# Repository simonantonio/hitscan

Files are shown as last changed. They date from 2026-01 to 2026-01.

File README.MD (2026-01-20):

# Project Hitscan

Hitscan logo

An attempt at a super cheap time keeping system for racers
It uses IR diodes on a drone, and a detection station to track when the drone passes the detector.

*Should?* be good at up to speeds of 200km/hr with a 200mm detection window - (need to actually validate this)

### IR Details
**Packet timing now:**

* SYNC: 270μs burst + 900μs gap = 1170μs
* 3 bits: ~300-600μs each = ~1200μs average
* **Total: ~2.3ms per packet**

**At 200mm cone width:**

* 100 km/hr (27.78 m/s): 7.2ms window = 3 packets ✅
* 150 km/hr (41.67 m/s): 4.8ms window = 2 packets ✅
* 200 km/hr: 3.6ms window = 1 packet ✅

> [!CAUTION]
> In development

Initial project is currently in the mail from the board fab.

## Tools

* Kicad 9.0 for board development
* PlatformIO for firmware builds and deployment

## Firmware
* [Base station](./hitscan-base/README.MD)
* [IR Blaster](./hitscan/README.MD)

### Web App
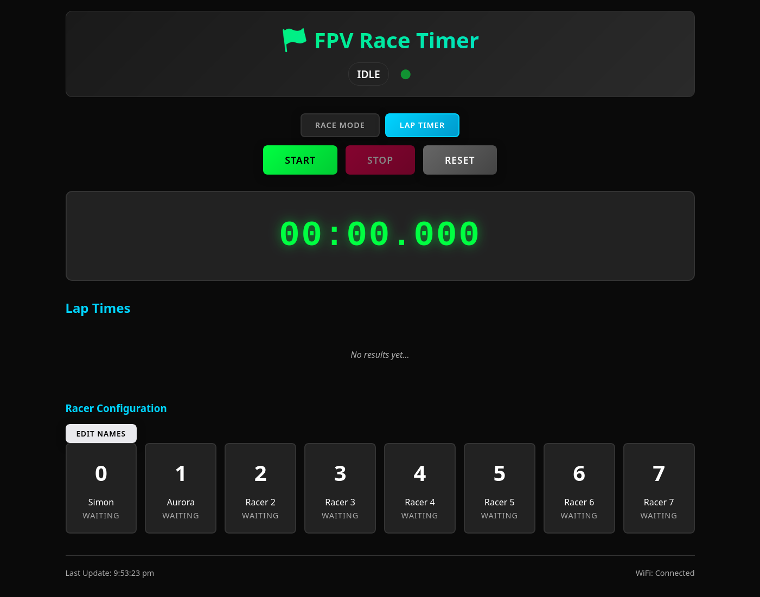
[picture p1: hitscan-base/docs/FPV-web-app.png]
Web app


## Hardware
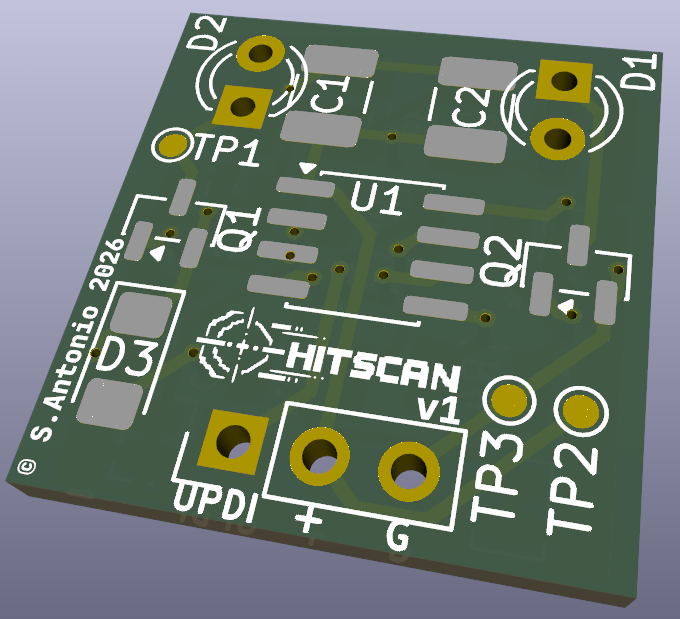
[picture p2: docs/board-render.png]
Board render


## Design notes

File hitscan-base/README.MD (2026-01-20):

# Hitscan base station

Runs on an ESP32 with Audio feedback, LED lights for status's and web app for tracking lap times
Mount your hitscan pcb on your quad with led's facing left/right on the quad. So tracking will work in either direction

Web app screenshot in Lap mode

> [!NOTE]
> Requires a 3d model (to be designed)

> [!WARNING]
> to be validated with actual hardware (PCB is in production)

> [!CAUTION]
> In development

## Thoughts
* Gate to be a tunnel looking at center at least 200mm long - thinking pvc pipe maybe. - ideally integrated with print
* runs IR detection on second core so it minimizes chances of missing a detection

## BOM
* [ESP32 Dev Kit](https://s.click.aliexpress.com/e/_c3kfkJBp) - any ESP32 dev board will do - you may have to tweak pins
* [MAX98357](https://s.click.aliexpress.com/e/_c2RRIQvD) - Class D Amplifier
* [Micro SD SPI breakout](https://s.click.aliexpress.com/e/_c3Uia44J)
* [16 Segment Pixel Ring](https://s.click.aliexpress.com/e/_c42eBGlp)
* [38khz TSOP4838](https://s.click.aliexpress.com/e/_c31xNmn9) - IR sensor

### Wiring diagram

> [!NOTE]
> TODO!

## Setup

### Environment
Set your local wifi password in `.env` file located alongside this readme

example:
```
WIFI_SSID=YOUR_HOME_NETWORK
WIFI_PASS=SUPER_SECURE_PASSWORD
```

### SPIFFS
Load the web app via platformio's `Build Filesystem Image` and `Upload Filesystem Image`

## Running

You can either navigate to .local or the devices ip, or you can connect to the hot spot created and connect there via browser

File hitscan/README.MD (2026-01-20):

# Hitscan board

> [!CAUTION]
> In development

This board gets mounted on your quad with +5v and GND, it emits a signal for up to 8 racers

Runs on ATTiny402 - fits on a 17.5mm x 18.5mm board

## Setup

Make sure to flash each pcb with different racer id

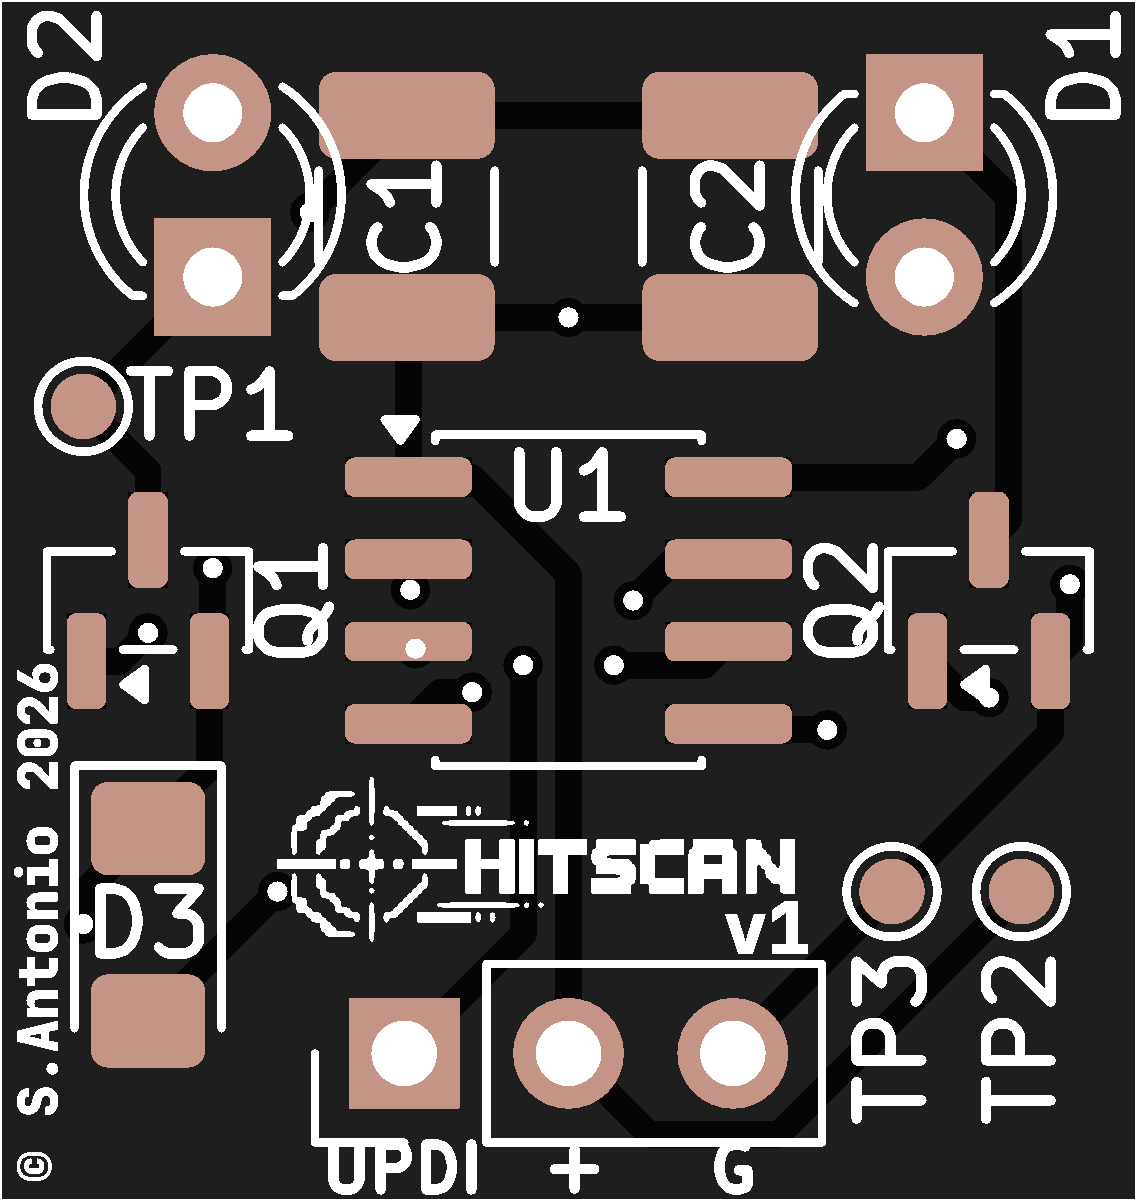
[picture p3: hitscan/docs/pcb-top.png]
PCB top


## What this firmware does

Blasts a single code for a racer over and over, ideally so when we cross our detection window we get at least 3 clean reads at speeds up to 200km/hr

Probably wont work outside in the sun.

## BOM
* [AO3400](https://s.click.aliexpress.com/e/_c3vhLHiB) - Mosfet to drive IR LEDs
* [TSAL4400](https://s.click.aliexpress.com/e/_c3m8pfAJ) - IR LED 100mA
* [ATTiny402](https://s.click.aliexpress.com/e/_c3q55ecr) - 8 pin 20mHz microcontroller
* [1210 SMD Resistors](https://s.click.aliexpress.com/e/_c2uIW28f) - misc resisters
* [UPDI Friend](https://s.click.aliexpress.com/e/_c4tdFiLV) - optional programmer for ATTiny
* [1210 Ceramic Capacitor](https://s.click.aliexpress.com/e/_c4kVavzV) - 0.1uF capacitor
* [1210 Ceramic Capacitor](https://s.click.aliexpress.com/e/_c3ftnBcb) - 100uF capacitor
* [1206 LEDs](https://s.click.aliexpress.com/e/_c4UlNysX) - optional colored LED for status

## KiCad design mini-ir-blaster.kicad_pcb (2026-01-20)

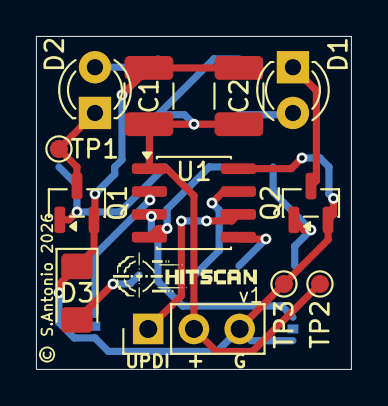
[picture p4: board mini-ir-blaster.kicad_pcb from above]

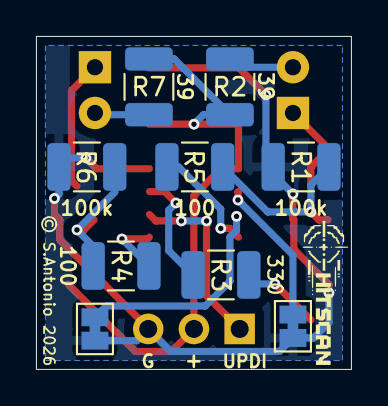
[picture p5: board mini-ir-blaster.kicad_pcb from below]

Board: 2 copper layers, 17.5 x 18.5 mm, 21 parts (9 on the bottom side), 15 nets.

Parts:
C1: 10uF; C_1210_3225Metric_Pad1.33x2.70mm_HandSolder
C2: 0.1uF; C_1210_3225Metric_Pad1.33x2.70mm_HandSolder
D1, D2: TSAL4400; LED_D3.0mm_IRBlack
D3: LED; LED_1206_3216Metric_Pad1.42x1.75mm_HandSolder
J1: Conn_01x03_Pin; PinHeader_1x03_P2.54mm_Vertical
JP2, JP3: Jumper_2_Bridged; SolderJumper-2_P1.3mm_Bridged_Pad1.0x1.5mm
Q1, Q2: AO3400A; SOT-23
R1, R6: 100k; R_1210_3225Metric_Pad1.30x2.65mm_HandSolder
R2, R7: 39; R_1210_3225Metric_Pad1.30x2.65mm_HandSolder
R3: 330; R_1210_3225Metric_Pad1.30x2.65mm_HandSolder
R4, R5: 100; R_1210_3225Metric_Pad1.30x2.65mm_HandSolder
TP1: IR1TP; TestPoint_Pad_D1.0mm
TP2: +TP; TestPoint_Pad_D1.0mm
TP3: GNDTP; TestPoint_Pad_D1.0mm
U1: ATtiny402-SS; SOIC-8_3.9x4.9mm_P1.27mm

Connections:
+5V: C1.1, C2.1, J1.2, R2.1, R7.1, TP2.1, U1.1 (VCC)
/PA1: R5.1, U1.4 (PA1)
/PA2: R4.1, U1.5 (PA2)
/UPDI: J1.1, U1.6 (~RESET/PA0)
GND: C1.2, C2.2, D3.1 (K), J1.3, JP2.2 (B), JP3.2 (B), Q1.2 (S), Q2.2 (S), R1.1, R6.1, TP3.1, U1.8 (GND)
unnamed: D1.2 (A), R7.2
unnamed: D1.1 (K), Q2.3 (D)
unnamed: D2.2 (A), R2.2
unnamed: D2.1 (K), Q1.3 (D), TP1.1
unnamed: D3.2 (A), R3.2
unnamed: JP2.1 (A), U1.2 (PA6)
unnamed: JP3.1 (A), U1.3 (PA7)
unnamed: Q1.1 (G), R1.2, R5.2
unnamed: Q2.1 (G), R4.2, R6.2
unnamed: R3.1, U1.7 (PA3)

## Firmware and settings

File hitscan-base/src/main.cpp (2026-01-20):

#include <Arduino.h>
#include "RaceTimerSystem.hpp"

// Pin definitions
#define IR_PIN 23
#define LED_PIN 25
#define I2S_BCK 26
#define I2S_WS 27
#define I2S_DATA 14

// WiFi credentials
const char *AP_SSID = "RaceTimer-01";  // Direct connection AP
const char *AP_PASSWORD = "racing123"; // AP password (min 8 chars)
const char *STA_SSID = WIFI_SSID;
const char *STA_PASSWORD = WIFI_PASS;

RaceTimerSystem raceTimer(IR_PIN, LED_PIN, I2S_BCK, I2S_WS, I2S_DATA);

void heartBeat()
{
  pinMode(2, OUTPUT);

  // thump
  for (int i = 0; i <= 255; i += 5)
  {
    analogWrite(2, i);
    delay(6);
  }

  // slight relax
  for (int i = 255; i >= 80; i -= 5)
  {
    analogWrite(2, i);
    delay(6);
  }

  delay(120);

  // fade out
  for (int i = 80; i >= 0; i -= 5)
  {
    analogWrite(2, i);
    delay(8);
  }
}

void setup()
{
  heartBeat();
  heartBeat();
  heartBeat();
  // Start in AP mode, optionally connect to home WiFi
  // To use AP-only mode, pass nullptr for STA credentials:
  // raceTimer.begin(AP_SSID, AP_PASSWORD);
  raceTimer.begin(AP_SSID, AP_PASSWORD, STA_SSID, STA_PASSWORD);
}

void loop()
{
  raceTimer.update();
}

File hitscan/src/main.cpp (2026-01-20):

#include <Arduino.h>

#define IR_PIN1 1        // PA1
#define IR_PIN2 2        // PA2
#define STATUS_LED_PIN 3 // PA3
#define RACER_ID 0       // ID 0 - 7

// 38kHz carrier: period = 26.3μs, half-period = 13.15μs
// ATtiny402 typically runs at 20MHz by default
// delayMicroseconds() handles the timing
#define CARRIER_HALF_PERIOD 13

void setup()
{
  pinMode(IR_PIN1, OUTPUT);
  pinMode(IR_PIN2, OUTPUT);
  pinMode(STATUS_LED_PIN, OUTPUT);

  digitalWrite(IR_PIN1, LOW);
  digitalWrite(IR_PIN2, LOW);
  digitalWrite(STATUS_LED_PIN, HIGH); //we booted and have power
}


// Generate 38kHz carrier for specified microseconds
void burstIR(uint16_t micros) {
  uint16_t cycles = micros / 26; // ~38kHz cycles to generate

  for(uint16_t i = 0; i < cycles; i++) {
    digitalWrite(IR_PIN1, HIGH);
    digitalWrite(IR_PIN2, HIGH);
    delayMicroseconds(CARRIER_HALF_PERIOD);
    digitalWrite(IR_PIN1, LOW);
    digitalWrite(IR_PIN2, LOW);
    delayMicroseconds(CARRIER_HALF_PERIOD);
  }
}

// Gap with no carrier
void gapIR(uint16_t micros) {
  digitalWrite(IR_PIN1, LOW);
  digitalWrite(IR_PIN2, LOW);
  delayMicroseconds(micros);
}

// Send sync burst (unique long gap)
void sendSync() {
  burstIR(270);  // Minimum safe burst
  gapIR(900);    // Unique long gap - never in data
}

// Send a data bit
void sendBit(uint8_t bit) {
  burstIR(270);  // Minimum burst
  if(bit) {
    gapIR(600);  // Long gap = 1
  } else {
    gapIR(300);  // Short gap = 0
  }
}

// Send complete racer ID packet
void sendPacket(uint8_t id) {
  sendSync();
  sendBit((id >> 2) & 1);  // Bit 2 (MSB)
  sendBit((id >> 1) & 1);  // Bit 1
  sendBit(id & 1);          // Bit 0 (LSB)
  // No inter-packet gap - continuous transmission
}

void loop() {
  // Continuously transmit racer ID back-to-back
  sendPacket(RACER_ID);
}

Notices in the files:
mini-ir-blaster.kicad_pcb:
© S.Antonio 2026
